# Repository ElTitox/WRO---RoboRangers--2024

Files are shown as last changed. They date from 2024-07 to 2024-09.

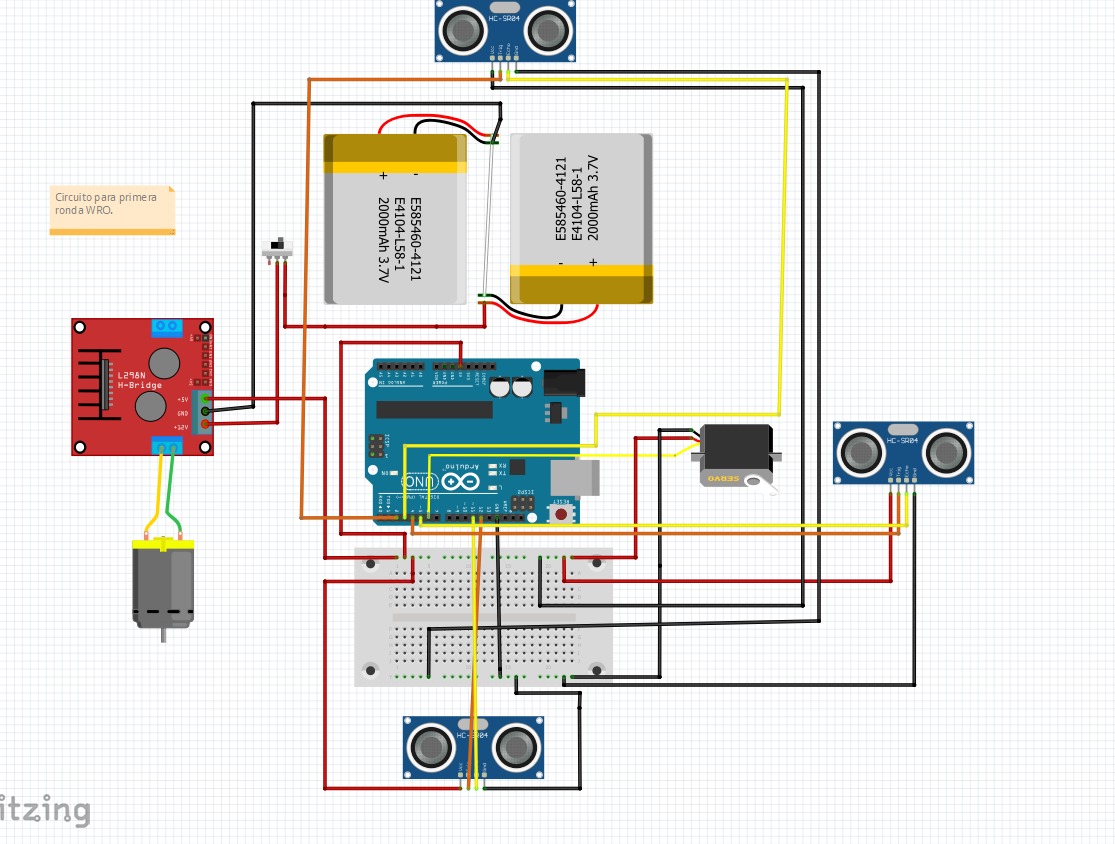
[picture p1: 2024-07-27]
schemes/Diseño_del_circuito_eléctrico.jpeg

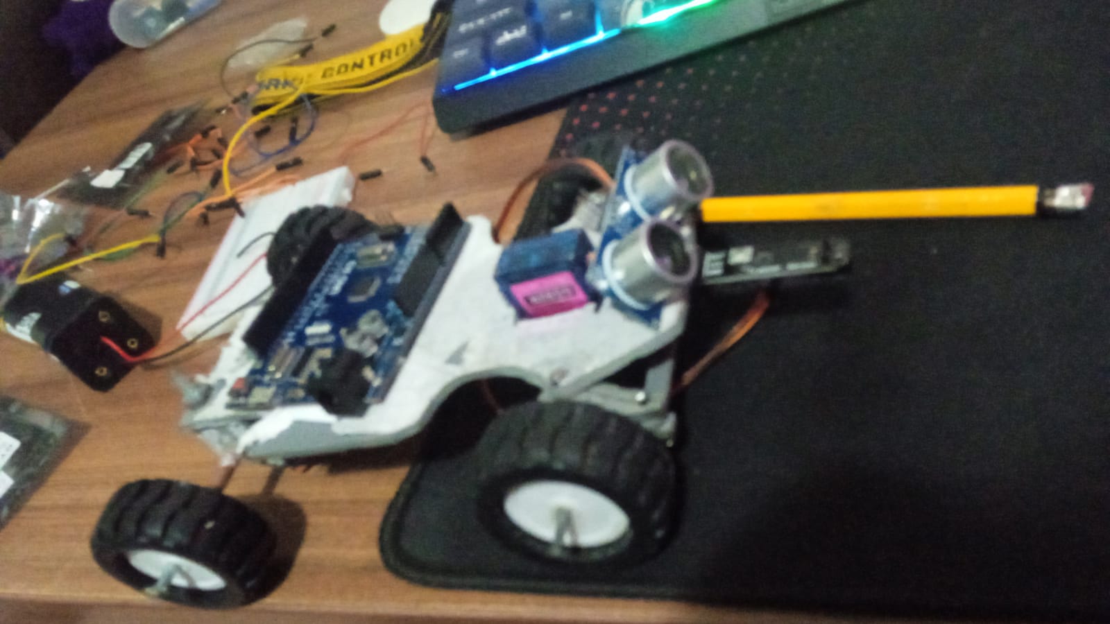
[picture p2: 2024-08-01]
other/proyecto-3.w.2.jpeg

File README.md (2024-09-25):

# Robo Rangers 

## Los integrantes del equipo son:
- Eldens Quintero  (Coordinador del equipo)  
- Hezir Corrales (Constructor del robot)
- Jose Gutierrez (Programador)
  
## Institución: Instituo América 
- Tutor: Hector Ortega
  
## Breve resumen del diseño:
Diseñamos el robot en sus inicios con distintos materiales como: ganchos de ropa, tubos de PVC, plastico de botella anticongelante y laminas de acrílico. Concluimos en diseñarlo con una lamina de placa perforada. Al inicio pensabamos en hacerlo de 15cm de largo, pero decidimos ampliar unos 3cm de largo y tenga un buen ancho para la bateria y sensores para que los demas componentes quepan de manera mas ordenada. LLegamos a diseñar nuestro sistema de dirección, más adelante entramos en detalles en los sistemas y programación del robot. 

### Materiales:                                                                                                                
-  PVC                                                                                                                         
-  Lamina de acrilico                                                                                                           
-  Placa perforada                                                                                                                  
-  Tornillos con sus tuercas                                                                                                    
-  Tacos azules para soporte                                                                                                   
-  Nanocinta acrílica doble contacto                                                                                            
-  Rollo de Estaño y Flux                                                                                                      
-  Clavos y tornillos                                                                                                           
-  Sunchos                                                                                                                      

### Herramientas:
-  Taladro con diferentes brocas y lijas
-  Arco Calar
-  Cautin
-  Destornilladores punta plana
-  Destornillador punta de estrella
-  Alicate
-  Pinza Pelacables
-  Pinza punta plana
-  multimetro

### Componentes:
-  base: hecha por una placa perforada
-  batería: 3 pilas recargables de litio conectadas en serie,de 200mah
-  sensores: 3 sensores ultrasónicos HC-S04, 1 sensor de color TCS3200
-  ARDUINO UNO R3
-  Servo: 1 servo motores SG90
-  Puente H L298N
-  Motor DC12V
-  Cables: Macho-Macho, Macho-Hembra y Cable Rígido
-  Switch on/off

## Procedimientos de contruccion del carro:

La [Construccion y el procedimiento del carro ](./other/) lo podemos encontrar en la carpeta other y el [diseño del carro ](./v-photos/) en la carpeta v-photos.

- Construcción de la base del carro:  
Usamos la placa fenólica (placa perforada) de base para nuestro coche, esta placa tambien nos sirve para hacer conexiones de cables con soldadura.
En ella colocamos un motor de 12V en la parte trasera, en el centro de la placa un Rack de pilas en serie (Rack de 3), 3 sensores ultrasonicos, 4 Taquillos plasticos azules atornillados en vertical desde abajo, y en la parte delantera un sistema de direccion hecha con PVC y operadas por un servo mediante un alambre de aluminio con el calibre suficiente para ser moldeado pero preferiblemente que sea duro.

- Colocación de elementos:  
Sobre el motor colocamos Puente H Doble con pegamento epoxy, los 4 tacos plasticos azules sirven de soporte para colocar un Arduino 1 R3 a su vez dan espacio para colocar y retirar las pilas con mayor facilidad.

  Los sensores ultrasonicos van colocado en los extremos Norte, Este y Oeste del carro midiendo la pista a los lados y delante.
  Los 2 sensores ultasonicos laterales van colocados en los bordes del Rack de la bateria con cinta adhesiva doble contacto y el sensor delantero es sostenido sobre un servo motor para que se mueva como un radar, colocado arriba del sensor de color. 

- Parte trasera del carro:  
El motor se modifico con una caja de cambio, esta se encuentra ubicada en la parte de atras y se mantiene en su lugar usando una corra de cuero atornillada a la placa fenólica y usando una tecnica de pegado con Pegamento (cianoacrilato) y Poliestireno.
En la parte inferior izquierda de la placa fenolica conectamos y soldamos todos los cables negativos (tierra común) y al otro lado todos los positivos de forma que la bateria alimenta al puenta H con un intervalo de 11.1V a 12.6V y a todo el circuito con 5V regulado por el puente H.

- Parte delantera del carro:  
El [sistema de direccion](schemes/Lanza_de_la_dirección_nueva.jpeg) esta hecha con PVC unidas con pegamento epoxy, usamos balineras y clavos para sostener y permitir el giro de las ruedas, por ultimo la Lanza de la direccion (hecha de PVC) y unida servo con un alambre para que está se mueva. El Servo sobresale por la parte superior para facilitar la conexion de los pines hacia el arduino y no estorbe en el giro del carro; ademas agregamos un sensor de color TCS3200 lo cual nos ayudara a la hora de la segunda ronda donde el carro tendra que dectectar los colores.

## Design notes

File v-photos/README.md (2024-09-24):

## Diseño del robot usado en la Regional

[Diseño trasero](a.Vista_trasera_del_robot1.jpeg) 

[Diseño de abajo](a.Vista_de_abajo_del_robot1.jpeg) 

[Diseño del lado derecho](a.Vista_del_lado_derecho_del_robot1.jpeg)

[Diseño del lado izquierdo](a.Vista_del_lado_izquierdo_del_robot1.jpeg)

[Diseño de arriba](a.Vista_de_arriba_del_robot1.jpeg)

[Diseño del frente](a.Vista_del_frente_del_robot1.jpeg)

## Diseño del robot para la Nacional

- Para el enfoque de este diseño nos basamos en el anterior pero con mejoras variadas:

[Diseño de abajo](Vista_de_abajo_del_robot2.jpg)
Algo a destacar es que la placa perforada atornillada a la plataforma principal del carro, esta plaquita se usa como union ya que la placa principal se partio en ese lado logrando unir de forma resistente las plataformas partidas. También el estado de las soldaduras y conexiones. La línea de alimentación positiva está de la parte izquierda y la línea de alimentación negativa está del lado derecho, estas lineas de alimentación tiene las conexiones que salen de cada componente.

[Diseño de arriba](Vista_de_arriba_del_robot2.jpg)
Lo que mas destaca es el arduino y las conexiones del arduino para los sensores, motores y la alimentación para el arduino. 

[Diseño del frente](Vista_del_frente_del_robot2.jpg)
Se aprecia el sistema de dirección del carro, hecha desde 0 con materiales de pvc y lamina de acrilico. La instalación del sensor ultrasonico que nos ayuda a medir la distancia de enfrente con las cual podemos seguir la logica de carro para la segunda ronda junto a al sensor de color.

[Diseño del lado derecho](Vista_del_lado_derecho_del_robot2.jpg)
Se observa en donde estan los componentes en el carro, ultrasonicos, puente H, la placa arduino y los espacios que toman estos mismos, las conexiones de alimentación y los pines para controlar cada componente, la forma de construcción del sistema de tracción y dirección del carro y la posición de las llantas. La instalación de un capacitor de 0.1 uF

[Diseño del lado izquierdo](Vista_del_lado_izquierdo_del_robot2.jpg)
De la misma forma que del lado derecho, lo unico a destacar es que no es igual al lado derecho, los sensores estan en una posicion diferente a los del lado derecho.

[Diseño trasero](Vista_trasera_del_robot2.jpg)
Como se puede observar, se diseño una tracción trasera con una caja de engranajes sacada de un carrito rc, modificada con un motor DC de hasta 12V , arriba de la caja esta puesto el puente H L298N. Mas al frente se nota la posición del arduino.

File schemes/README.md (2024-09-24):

# Diagramas Electromecánicos
### Podran ver en fotos y archivos los esquemas de la propia plataforma del robot, del sistema de dirección y del circuito eléctrico. 

## Esquemático y diseño del circuito eléctrico
Para hacer el esquemático usamos el software Fritzing, si desea ver con mas detalle o modificar el circuito deberá de tenerlo descargado. Descargar Fritzing: https://fritzing.org/download

[Archivo del circuito](./Fritzing/Primera_ronda_wro.fzz) Descarga del archivo del circuito eléctrico.

[Imagen del circuito](./Fritzing/Primera_ronda_wro.fzz.jpeg) Imagen del archivo del circuito eléctrico.

[Diseño del circuito eléctrico](Diseño_del_circuito_eléctrico.jpeg)
El diseño es muy parecido al setup real del circuito, la única diferencia es el medio en donde fueron construidos el real en placa perforadas y este con ayuda de una protoboard.

[Esquematico del circuito eléctrico](Esquematico_del_circuito.jpeg)
Una vista mas clara de cada modelo de forma esquematica y sus conexiones.

## Diagramas del chasis y el sistema de dirección
Estos diagramas no tienen su medición en las fotos, las mediciones están en la descripción de cada foto. Los diagramas se hicieron en una hoja milímetrada, cada cuadrado mide 0.5cm. Para la dirección nos inspiramos en hacerla de este video: https://www.youtube.com/watch?v=0pgU9oZoR14

[Diagramas del carro](Chasis_de_la_plataforma_del_carro_y_soportes_de_la_dirección.jpeg)
Se dividen en 3 piezas, plataforma del carro, rectangulos en paralelo y piezas de forma circular al final dibujadas en la parte delantera de la plataforma:
-  La plataforma tiene un largo de 17.5cm, al principio se penso hacerlo de 15cm, pero para solucionar problemas de espacio se decidio ampliar el largo, el ancho del frente y atras es de 7cm y el ancho del medio es de 9cm.
-  Los rectángulos que estan dibujados de forma paralela miden 2.6cm de largo y 0.7cm de ancho.
-  Las piezas dibujadas junto con la parte delantera del chasis y las ruedas, sostienen las piezaz de la balineras, son 4 piezas que hacer, en la parte de arriba y abajo. Esta pieza mide 2.3cm de largo y 0.8cm de ancho.

[Pieza de la balinera](Pieza_para_la_balinera.jpeg)
Mediciones de cada parte de la pieza:
-  La pieza tiene un diametro de 2.3cm, el círculo grande del medio (no el chico) tiene un diametro de 1.8cm. El círculo grande del medio va vacío ya que este círculo es donde va la balinera.
-  Las patitas sobresalientes donde va la lanza tienen un ancho de 0.3cm, el espacio que los separa es de 0.4cm y un largo de 1cm, tanto como la patita como el espacio vacío.

[Diseño de la lanza](Lanza_de_la_dirección_anterior.jpeg)
La lanza tiene un largo de 8cm y un ancho de 0.8cm ademas de la lanza anterior para el nuevo diseño del carro nos guiamos de la misma, para hacer el [diseño de la lanza nueva.](Lanza_de_la_dirección_nueva.jpeg).

[MRU](Movimiento_rectilíneo_uniforme.jpeg)
para calcular la velocidad lineal usamos un metro y pusimos la punta del carro en el inicio del metro y calculamos el tiempo en el recorria el metro, nos dio los siguiente resultados: 75,85 y 88 milisegundos de ellos sacamos el promedio que fue 83 y tener un aproximado de velocidad; llegamos a la conclución que la velocidad maxima del carrito es 1.20m/s. 

## 1. Especificaciones Electrónicas
- **Motor DC:**
  - Voltaje nominal: 12V
- **Batería:**
  - Conexión: En serie
  - Voltaje de cada pila: 3.7V
  - Capacidad de cada pila: 3200 mAh
- **Microcontrolador:**
  - Tipo: Arduino R3
- **Sensores:**
  - Sensores ultrasónicos: 3
  - Sensor de color: 1 

---

## 2. Especificaciones Mecánicas
- **Sistema de Engranajes:**
  - **Primera Etapa: Motor a Primer Engranaje**
    - Engranaje motor:
      - Dientes: 8
    - Engranaje conducido:
      - Dientes: 12
    - Relación de Transmisión (RT1):
      - RT1 = Dientes del engranaje conducido / Dientes del engranaje motor
      - RT1 = 12 / 8 = 1.5
  - **Segunda Etapa: Engranaje de 30 Dientes**
    - Engranaje motor:
      - Dientes: 30
    - Engranaje conducido:
      - Dientes: 30
    - Relación de Transmisión (RT2):
      - RT2 = Dientes del engranaje conducido / Dientes del engranaje motor
      - RT2 = 30 / 30 = 1
- **Relación de Transmisión Total (RT Total):**
  - RT total = RT1 × RT2
  - RT total = 1.5 × 1 = 1.5
- **Torque:**
  - Torque ajustado = Torque a 12V × (10 / 12)
  - Torque en las llantas = Torque ajustado × 1.5

## Desglose de Corrientes en mA anterior
- Arduino Uno R4: ~70 mA
- Sensor ultrasónico HC-SR04: ~15 mA
- Puente H L298N: ~30 mA
- Motor DC: ~250 mA 
- Servo SG-92: ~250 mA (en movimiento)

### Cálculo del Consumo Total de Corriente
- Arduino Uno R4: 70 mA
- 3 Sensores ultrasónicos HC-SR04: 3 * 15 mA = 45 mA
- Puente H L298N: 30 mA
- Motor DC: 250 mA
- Servo SG-92: 250 mA

Consumo total: 655mA

## Actualización del Desglose de Corrientes en mA
- Arduino Uno R3: ~50 mA
- Sensor ultrasónico HC-SR04: ~15 mA
- Puente H L298N: ~30 mA
- Motor DC: ~250 mA
- Servo SG-92: ~250 mA (en movimiento)

### Cálculo del Consumo Total de Corriente
- Arduino Uno R3: 50 mA
- 3 Sensores ultrasónicos HC-SR04: 3 * 15 mA = 45 mA
- Puente H L298N: 30 mA
- Motor DC: 250 mA
- Servo SG-92: 250 mA

Consumo total: 50 + 45 + 30 + 250 + 250 = 625 mA

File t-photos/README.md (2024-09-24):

Fotos del equipo
====

Este directorio contiene 3 fotos del equipo (una oficial, una con el carrito y una foto divertida con todos los miembros del equipo)

[- foto oficial de competencia](foto_oficial_inauguración.jpg)

[- foto del equipo](foto_del_equipo.jpg)

[- foto con el carrito](foto_con_el_carrito.jpeg)

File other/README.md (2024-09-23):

[Diseño Inicial](proyecto-1.inicial-del-carro.jpeg) 
En los inicios de este proyecto, tuvimos la idea de empezar la base de nuestro carro con un gancho de ropa moldeado a medida de la base dibujada, mas esta idea fue descartada pues no tenia la suficiente rigidez.

[Diseño Numero-2](proyecto-2.segunda-base.jpeg) 
Durante la cosntruccion de nuestra segunda idea buscamos una base que no fuera ni tan pesa pero rigida y pensamos en un platico de una botella de anticongelante la probamos, pero durante el proceso de la construccion de este carro vimos como se undia por el peso y descartamos la idea pues no era lo suficientemente rigido.

[Diseño Numero-3](proyecto-3.tercera-base.jpeg)
En la tercera prueba de nuestro proyecto pensamos en un tubo de pv, pero para lograr usarlo de plataforma tuvimos que moldearlo con el debido cuidado y serrucharlo a la medida de la base para usarlo

[Diseño 3.1](proyecto-3.w.1.jpeg)
Vimos que la base funcionaba bien pues era lo sufientemente rigida para soportar los componentes.

[Diseño 3.2](proyecto-3.w.2.jpeg)
Pensamos en trabajar con ella y nos pusimos manos a la obra con esta base para tenerla lista a la hora de la presentacion del carro.

[Diseño 3.3](proyecto-3.w.3-ultimo.jpeg)
Este fue el proyecto presentado a nuestras primeras olimpiadas e inaguracion, pero durante la competencia nos fallaron muchas cosas como el arduino las baterias y algunos pines por ende descartamos la idea y pensamos en una base funcional pero a la vez rigida

[Diseño Numero-4](proyecto-4.cuarta-base.jpeg)
y por ultimo la encontramos una base totalmente funcional y que pudiera soportar lo componente ya solo es de probar todos los componenetes que funcionen de la devida manera a la hora de la competencia y tener los programas listos.

[Diseño Final Regional](proyecto-final1-del-carro-regional.jpeg)
tenemos el diseño final de las regional el cual fue nuestro carro; este diseño ha sido creado con el objetivo de mejorar la funcionalidad y el rendimiento en la pista, incorporando las modificaciones necesarias para asegurar su operatividad y eficacia, ademas de ser el diseño final utilizado en las regionales

[Diseño Final Nacional](proyecto-final2-del-carro-nacional.jpg)
con esta estructura logramos realizar un carro que pueda competir a nivel nacional, optimizando su diseño en términos de velocidad, estabilidad y eficiencia mecánica. Este diseño final toma en cuenta los aspectos observados en los prototipos anteriores, incorporando mejoras para maximizar el rendimiento en pista segun los obstaculos que se le presente.

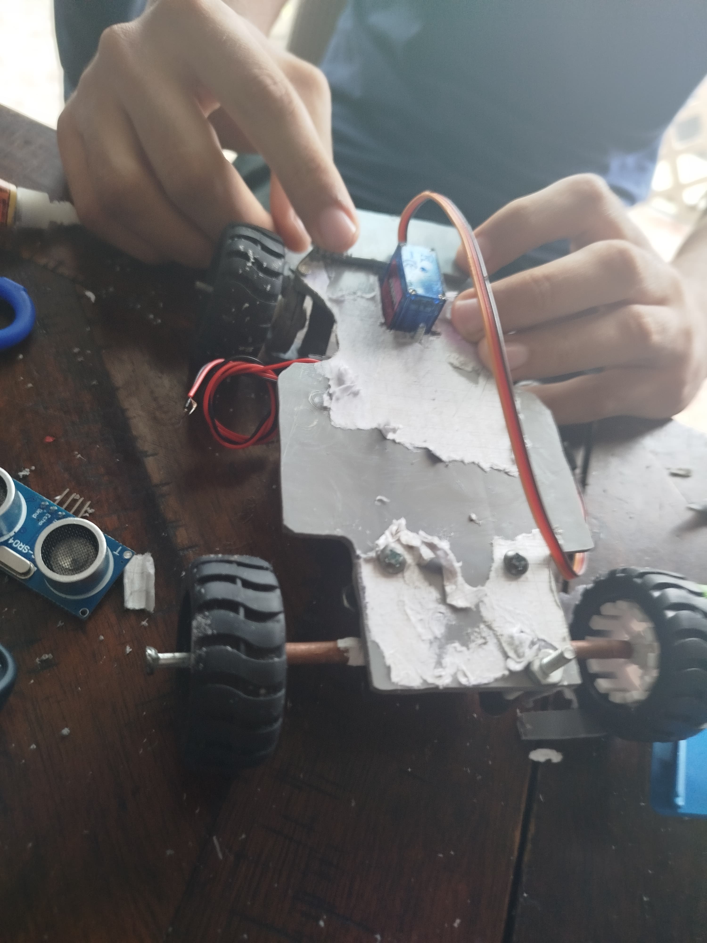
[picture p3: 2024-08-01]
other/proyecto-3.w.1.jpeg

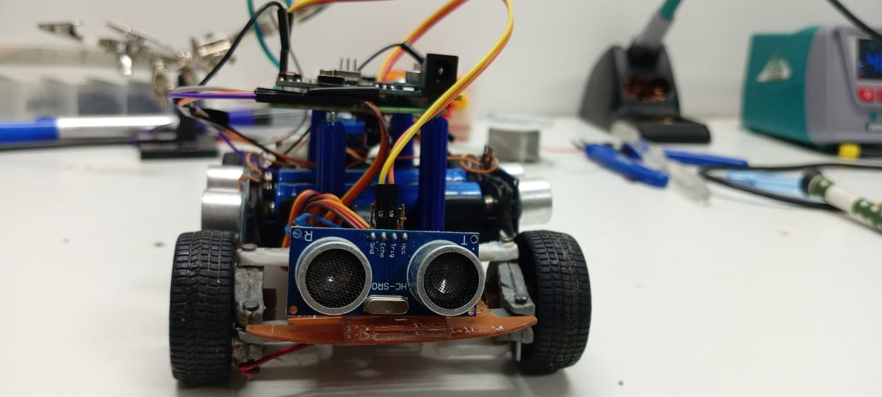
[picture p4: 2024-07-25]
v-photos/a.Vista_del_frente_del_robot1.jpeg

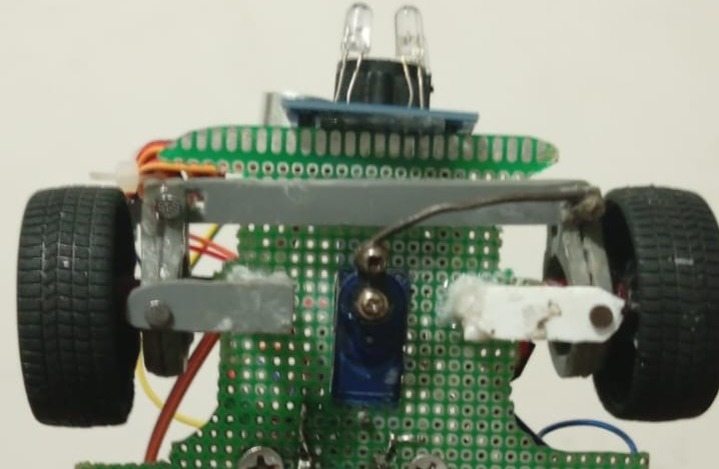
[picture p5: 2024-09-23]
schemes/Lanza_de_la_dirección_nueva.jpeg

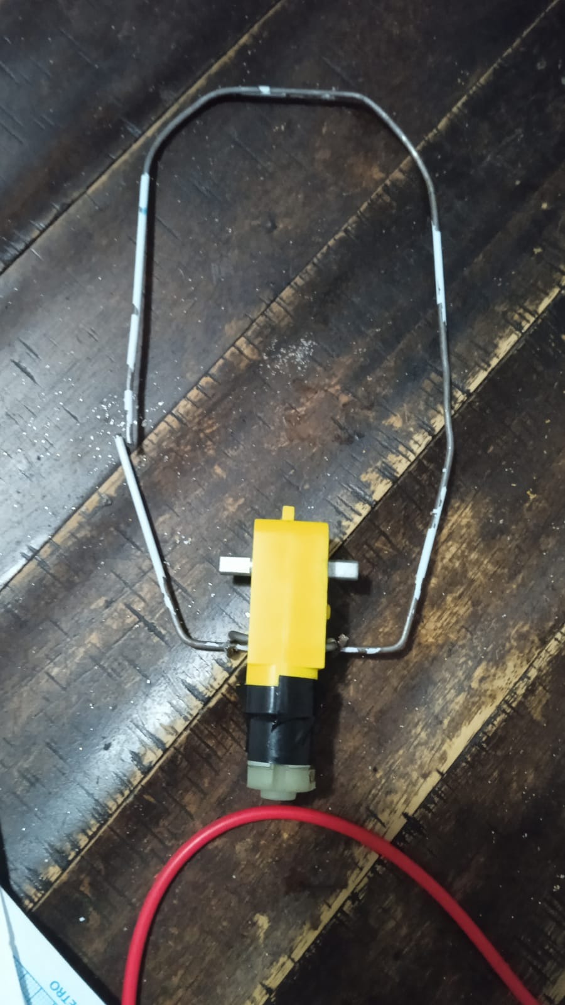
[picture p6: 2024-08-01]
other/proyecto-1.inicial-del-carro.jpeg

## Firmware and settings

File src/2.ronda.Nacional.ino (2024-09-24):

#include <Servo.h>

// Pines del puente H L298N para el motor DC
const int enB = 9;
const int in3 = 8;
const int in4 = 7;

// Servo motor
Servo servoMotor;
const int servoPin = 6;  // Pin del servo motor

// Variables de rotación
const int RotacionInicialServo = 78;  // Ángulo inicial del servo motor

// Pines de los sensores ultrasónicos
#define TRIG_PIN_R 2
#define ECHO_PIN_R 3
#define TRIG_PIN_L 12
#define ECHO_PIN_L 11
#define TRIG_PIN_F 4  // Definir el pin TRIG para el sensor frontal
#define ECHO_PIN_F 5  // Definir el pin ECHO para el sensor frontal

// Pines del sensor de color TCS3200
const int S0 = A0;  
const int S1 = A1;  
const int S2 = A2;  
const int S3 = A3;  
const int salidaTCS = A4; 
const int ledPin = 13;  

// Variable para controlar si la lógica ya fue ejecutada
bool logicaEjecutada = false;

// Constantes para las rotaciones
const int RotacionesPorTiempo = 100;  // Constante de rotación por tiempo

void setup() {
  // Configuración de los pines del puente H
  pinMode(enB, OUTPUT);
  pinMode(in3, OUTPUT);
  pinMode(in4, OUTPUT);

  // Configuración del servomotor
  servoMotor.attach(servoPin);
  servoMotor.write(RotacionInicialServo);  // Servo recto a 78°

  // Configuración de los pines de los sensores ultrasónicos
  pinMode(TRIG_PIN_R, OUTPUT);
  pinMode(ECHO_PIN_R, INPUT);
  pinMode(TRIG_PIN_L, OUTPUT);
  pinMode(ECHO_PIN_L, INPUT);
  pinMode(TRIG_PIN_F, OUTPUT);  // Configurar TRIG del sensor frontal
  pinMode(ECHO_PIN_F, INPUT);    // Configurar ECHO del sensor frontal
  
  // Configuración del sensor de color
  pinMode(S0, OUTPUT);		// pin 4 como salida
  pinMode(S1, OUTPUT);		// pin 5 como salida
  pinMode(S2, OUTPUT);		// pin 6 como salida
  pinMode(S3, OUTPUT);		// pin 7 como salida
  pinMode(salidaTCS, INPUT);	// pin 8 como salida
  
  digitalWrite(S0,HIGH);	// establece frecuencia de salida
  digitalWrite(S1,LOW);		// del modulo al 20 por ciento
  
  // Inicialización del Serial (opcional, para debug)
  Serial.begin(9600);
  Serial.println("Iniciando el sistema...");
}

// Función para medir distancia (en centímetros)
float measureDistance(int trigPin, int echoPin) {
  digitalWrite(trigPin, LOW);
  delayMicroseconds(2);
  digitalWrite(trigPin, HIGH);
  delayMicroseconds(10);
  digitalWrite(trigPin, LOW);

  long duration = pulseIn(echoPin, HIGH);
  float distance = (duration / 2.0) / 58.0;  // Conversión a centímetros
  return distance;
}

// Función para medir distancia basada en la dirección
float measure(char C) {
  if (C == 'R') {
    return measureDistance(TRIG_PIN_R, ECHO_PIN_R);
  } else if (C == 'L') {
    return measureDistance(TRIG_PIN_L, ECHO_PIN_L);
  } else if (C == 'F') {
    return measureDistance(TRIG_PIN_F, ECHO_PIN_F); // Medir el frente
  }
  return -1; // Si no es una dirección válida
}

// Función de movimiento al máximo
void movimientoMaximo() {
  Serial.println("Moviendo hacia adelante a máxima velocidad...");
  digitalWrite(in3, LOW);
  digitalWrite(in4, HIGH);  // Motor hacia adelante
  analogWrite(enB, 255);    // Velocidad máxima del motor
}

// Función para mover hacia atrás
void moveBack(int rotaciones) {
  int tiempoDeRotacion = rotaciones * RotacionesPorTiempo;
  Serial.println("Moviendo hacia atrás...");
  
  // Mover hacia atrás
  digitalWrite(in3, HIGH);
  digitalWrite(in4, LOW);
  // Iniciar el motor a velocidad máxima
  analogWrite(enB, 255);
  
  delay(tiempoDeRotacion);  // Esperar el tiempo de rotación

  // Apagar el motor al finalizar
  analogWrite(enB, 0);
  Serial.println("Movimiento hacia atrás completado.");
}

// Función para girar rápidamente a la derecha
void rotateRightFast(int rotaciones) {
  int tiempoDeRotacion = rotaciones * RotacionesPorTiempo;
  Serial.println("Girando rápidamente a la derecha...");
  servoMotor.write(180);
  delay(tiempoDeRotacion);  // Tiempo de giro
  Serial.println("Giro a la derecha completado.");
}

// Función para la lógica del giro y decisiones
void logicaMovimiento() {
  // El servo gira 65° para iniciar el giro
  Serial.println("Iniciando movimiento lógico...");
  servoMotor.write(62);  
  delay(500);  // Espera a que el servo complete el giro

  // Encender el motor por 200 milisegundos
  analogWrite(enB, 255);
  digitalWrite(in3, LOW);
  digitalWrite(in4, HIGH);  // Motor hacia adelante
  delay(250);  // Motor encendido por 250 ms
  
  // Apagar el motor
  analogWrite(enB, 0);
  servoMotor.write(88);

  // El carro continuará girando por inercia 82°
  delay(500);  // Simular inercia

  // Medir la distancia frontal
  float distanciaFrontal = measure('F');
  Serial.print("Distancia al frente: ");
  Serial.println(distanciaFrontal);

  // Si la distancia es mayor a 100 cm (1 metro), cambiar de línea
  if (distanciaFrontal > 25.0) {
    Serial.println("Distancia mayor a 100 cm, cambiar de línea.");
    // Llamar a la corrección de línea
    lineCorrection();
  } else {
    analogWrite(enB, 0);
    Serial.println("Distancia menor a 100 cm, implementar lógica después.");

    // Sensor de color
    digitalWrite(S2, LOW);			// establece fotodiodos con filtro rojo
    digitalWrite(S3, LOW);			
    int rojo = pulseIn(salidaTCS, LOW);	
    delay(200);				// demora de 200 mseg
    
    digitalWrite(S2, HIGH);		// establece fotodiodos con filtro verde
    digitalWrite(S3, HIGH);		
    int verde = pulseIn(salidaTCS, LOW);	
    delay(200);				// demora de 200 mseg
    
    digitalWrite(S2, LOW);			// establece fotodiodos con filtro azul
    digitalWrite(S3, HIGH);		
    int azul = pulseIn(salidaTCS, LOW);	
    delay(200);				// demora de 200 mseg
    
    Serial.print("R:");			
    Serial.print(rojo);			
    Serial.print("\t");			
    
    Serial.print("V:");			
    Serial.print(verde);			
    Serial.print("\t");			

    if (rojo < 208 && verde > 428 && azul > 312) {		
      Serial.println("ROJO");				
      // Imprimir mensaje cuando se identifica el rojo
      Serial.println("¡Se detectó el color ROJO!");  
      // Gira 62° y luego retrocede
      servoMotor.write(62);  
      delay(700);  // Esperar que el servo complete el giro
      moveBack(3.5);  // Llamar a moveBack con 3.5 rotaciones
      analogWrite(enB, 0); // Detener el carro después de retroceder
    } 
    else if (verde < 541 && rojo > 446 && azul > 347) {	
      Serial.println("VERDE");				
      // Imprimir mensaje cuando se identifica el verde
      Serial.println("¡Se detectó el color VERDE!");  
      // Gira 110° y luego retrocede
      servoMotor.write(110);  
      delay(700);  // Esperar que el servo complete el giro
      moveBack(3.5);  // Llamar a moveBack con 3.5 rotaciones
      analogWrite(enB, 0); // Detener el carro después de retroceder
    }
  }
}

// Función para la corrección de línea
void lineCorrection() {
  Serial.println("Iniciando corrección de línea...");
  rotateRightFast(100);  // Rotar rápidamente
  delay(500);  // Esperar que el servo complete el giro

  // Después de la corrección, reanudar el movimiento
  movimientoMaximo();
}

// Función principal loop
void loop() {
  // Medir la distancia del sensor frontal
  float distanciaFrontal = measure('F');

  // Si la distancia es menor a 100 cm, activar la lógica
  if (distanciaFrontal < 100 && !logicaEjecutada) {
    logicaEjecutada = true;  // Evitar que la lógica se ejecute múltiples veces
    logicaMovimiento();
  } 
  else if (distanciaFrontal >= 100) {
    logicaEjecutada = false;  // Reiniciar la lógica cuando la distancia es segura
    movimientoMaximo();
  }
}

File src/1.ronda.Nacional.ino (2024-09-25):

#include <Servo.h>

#define TRIG_PIN_R 2
#define ECHO_PIN_R 3
#define TRIG_PIN_L 12
#define ECHO_PIN_L 11
#define SERVO_PIN 6

Servo servoMotor;

const int enB = 9;
const int in3 = 8;
const int in4 = 7;

long duration;
float distanceR;
float distanceL;

bool haDetectadoLado = false;
bool giroDerecha = false;  // Indica si el giro es a la derecha

void setup() {
  Serial.begin(9600);

  pinMode(enB, OUTPUT);
  pinMode(in3, OUTPUT);
  pinMode(in4, OUTPUT);

  servoMotor.attach(SERVO_PIN);

  pinMode(TRIG_PIN_R, OUTPUT);
  pinMode(ECHO_PIN_R, INPUT);
  pinMode(TRIG_PIN_L, OUTPUT);
  pinMode(ECHO_PIN_L, INPUT);

  servoMotor.write(90);
  moveForward();
  delay(480);
  
  stopMotor(); // Motor detenido indefinidamente al inicio
}

void loop() {
  // El motor está detenido hasta que se detecte una distancia
  if (!haDetectadoLado) { // Es una condición para controlar el estado del motor, en este caso la condicion se hace cierta si detecto algun lado, se puede ver posteriormente en el loop una decisión para cambiar de estado esta variable.
    // Medir distancias
    distanceR = measure('R') + 2.50; // Error de medidda en el lado derecho
    distanceL = measure('L') + 2.50; // Error de medida en el lado izquierdo

    Serial.print("Distancia Derecha: "); // Impresiones para conocer el estado del ultrasonico derecho
    Serial.println(distanceR);  // Medición de la distancia del ultrasonico derecho
    Serial.print("Distancia Izquierda: "); // Impresiones para conocer el estado del ultrasonico izquierdo
    Serial.println(distanceL);  // Medición de la distancia del ultrasonico izquierdo

    // Comprobar si alguna distancia cumple la condición para girar
    if ((distanceR > 90 && distanceR < 900) || (distanceL > 90 && distanceL < 900)) { // Ésta decisión tiene condiciones con intervalos debido a tomar una posible medición de una esquina
      haDetectadoLado = true; // Una vez se cumpla cualquiera de las 2 condiciones esta variable se activa en true y 
      Serial.println("Giro detectado");

      // Determinar dirección del giro
      if (distanceR > 90 && distanceR < 900) {
        giroDerecha = true;
        servoMotor.write(180);  // Gira a la derecha
        moveForward();         // Avanzar mientras gira
        delay(550);
        servoMotor.write(90);

      } else if (distanceL > 90 && distanceL < 900) {
        giroDerecha = false;
        servoMotor.write(0);    // Gira a la izquierda
        moveForward();           // Avanzar mientras gira
        delay(450);
        servoMotor.write(90);
      }

      // Detener el motor y ajustar el servo
      stopMotor();             
      delay(600);              // Esperar medio segundo

      // Activar el motor y girar el servo simultáneamente
      analogWrite(enB, 255);  // Encender el motor a velocidad máxima

      // Ejecutar el bucle de avanzar y girar
      for (int i = 0; i < 11; i++) {
        moveForward();  // Avanzar indefinidamente
        delay(900);    // Esperar 0.9 segundos

        // Girar en la dirección determinada inicialmente
        if (giroDerecha) {
          servoMotor.write(180);  // Gira a la derecha
          delay(600);             // Mantener giro por 0.6 segundos
        } else {
          servoMotor.write(0);    // Gira a la izquierda
          delay(600);             // Mantener giro por 0.6 segundos
        }
        servoMotor.write(90);     // Ajustar el servo a la posición recta
      }

      // Detener el motor indefinidamente
      stopMotor();
      while (true);  // Pausar el motor indefinidamente
    }
  }
}

// Función para medir la distancia
float measureDistance(int trigPin, int echoPin) {
  digitalWrite(trigPin, LOW);
  delayMicroseconds(2);
  digitalWrite(trigPin, HIGH);
  delayMicroseconds(10);
  digitalWrite(trigPin, LOW);

  duration = pulseIn(echoPin, HIGH);
  return (duration / 2.0) / 29.1;  // Conversión
}

float measure(char C) {
  return (C == 'R') ? measureDistance(TRIG_PIN_R, ECHO_PIN_R) : measureDistance(TRIG_PIN_L, ECHO_PIN_L);
}

// Función para avanzar el robot
void moveForward() {
  analogWrite(enB, 255);  // Velocidad máxima
  digitalWrite(in3, LOW);
  digitalWrite(in4, HIGH);
}

// Función para detener el motor
void stopMotor() {
  analogWrite(enB, 0);  // Detener el motor
  digitalWrite(in3, LOW);
  digitalWrite(in4, LOW);
}

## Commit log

2024-07-25 Subida de fotos del vehiculo
    6 fotos añadidas
2024-07-25 Rename Vista de arriba del robot.jpeg to Vista del lado izquierdo del robot 3 .jpeg
2024-07-25 Perspectiva de todos los lados del robot
2024-07-25 Rename Vista de abajo del robot.jpeg to Vista_de_abajo_del_robot.jpeg
2024-07-25 Rename Vista de arriba del robot.jpeg to Vista_de_arriba_del_robot.jpeg
2024-07-27 Diseño del circuito eléctrico
2024-07-27 Rename 3870d32c-1bf2-4c80-ba2e-4bdc9b87c49a.jpeg to Diseño del circuito eléctrico.jpeg
2024-07-27 Rename Diseño del circuito eléctrico.jpeg to Diseño_del circuito_eléctrico.jpeg
2024-07-27 Rename Diseño_del circuito_eléctrico.jpeg to Diseño_del circuito_electrico.jpeg
2024-07-27 Rename Diseño_del circuito_electrico.jpeg to Diseno_del circuito_electrico.jpeg
2024-07-27 Rename Diseno_del circuito_electrico.jpeg to Diseño_del_circuito_eléctrico.jpeg
2024-07-27 Rename Primera ronda wro.fzz to Primera_ronda_wro.fzz
    [Primera_ronda_wro.fzz]
2024-07-27 Path Change
    [Primera_ronda_wro.fzz]
2024-08-01 SRC Updated
    Comentario añadidos en diferentes secciones del codigo y arreglos en el mismo para mejorar su comprensión.
